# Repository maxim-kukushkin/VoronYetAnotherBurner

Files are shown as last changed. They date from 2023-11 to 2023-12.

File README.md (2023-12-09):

# Description

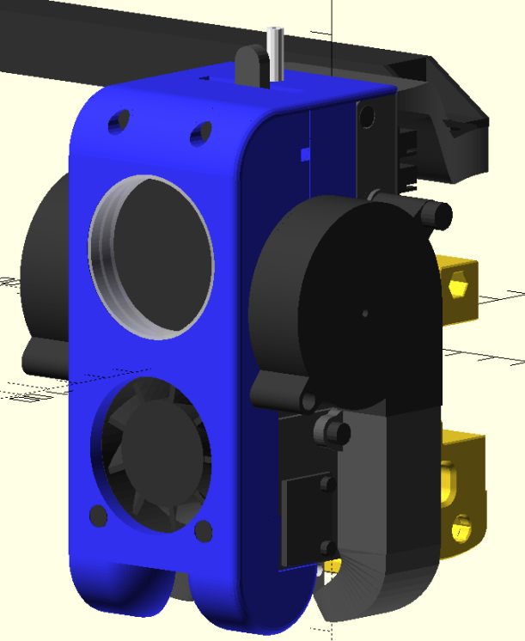
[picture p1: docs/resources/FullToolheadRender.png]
Full assembly render


YetAnotherBurner is (as the name suggests) yet another attempt to design a toolhead for Voron Trident (and 2.4) 3D printers. The main concern the author had about the existing solutions are:
- Usage of custom extruders
- Lack of attention to the part cooling (making it impossible to print PLA overhangs with the printer doors closed)
- Lack of LEDs or Trident support in some of the alternative projects

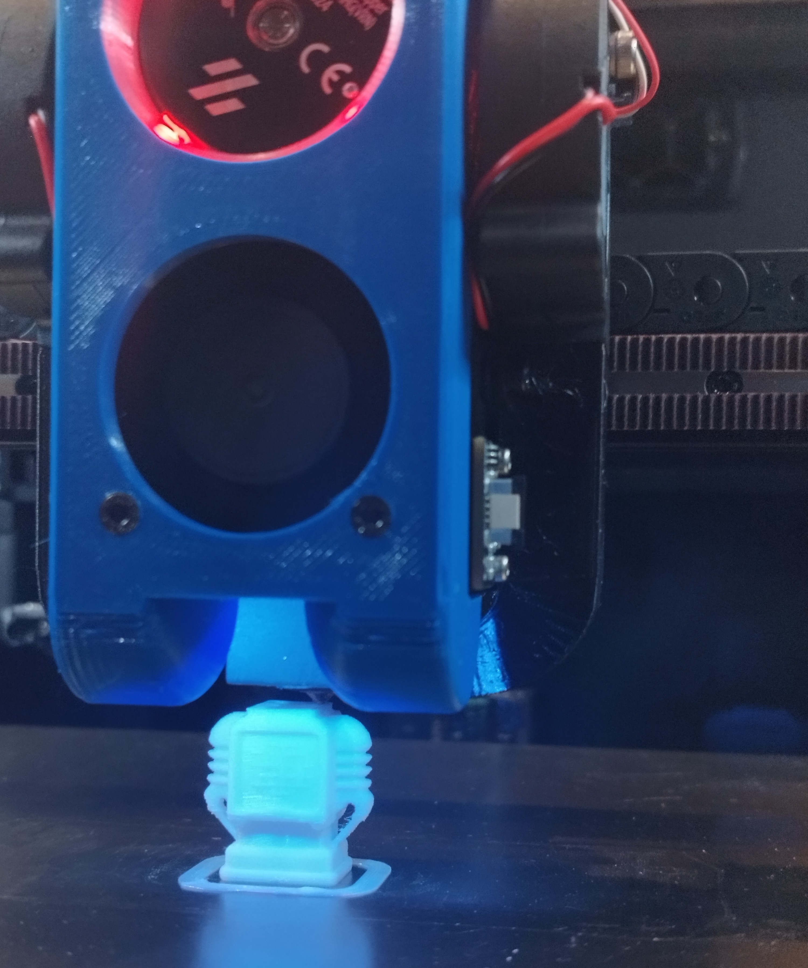
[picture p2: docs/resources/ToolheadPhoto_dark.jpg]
Toolhead photo (dark)


The features of this solution are:
- Strong part cooling (using 2x 5015 blower fans)
- Support of LEDs (2x part highlight + 4x status LEDs at the top)
- Usage of an existing extruder (BondTech LGX Lite)
- Easy loading of the filament + good grip of the bowden tube (by the extruder itself)
- Support of the toolhead breakout PCBis (same PCBs as used in Stealthburner)
- Support of ADXL345 accelerometer mounting
- Doesn't interfere with KlickyProbe, so it can be used as normal with this toolhead

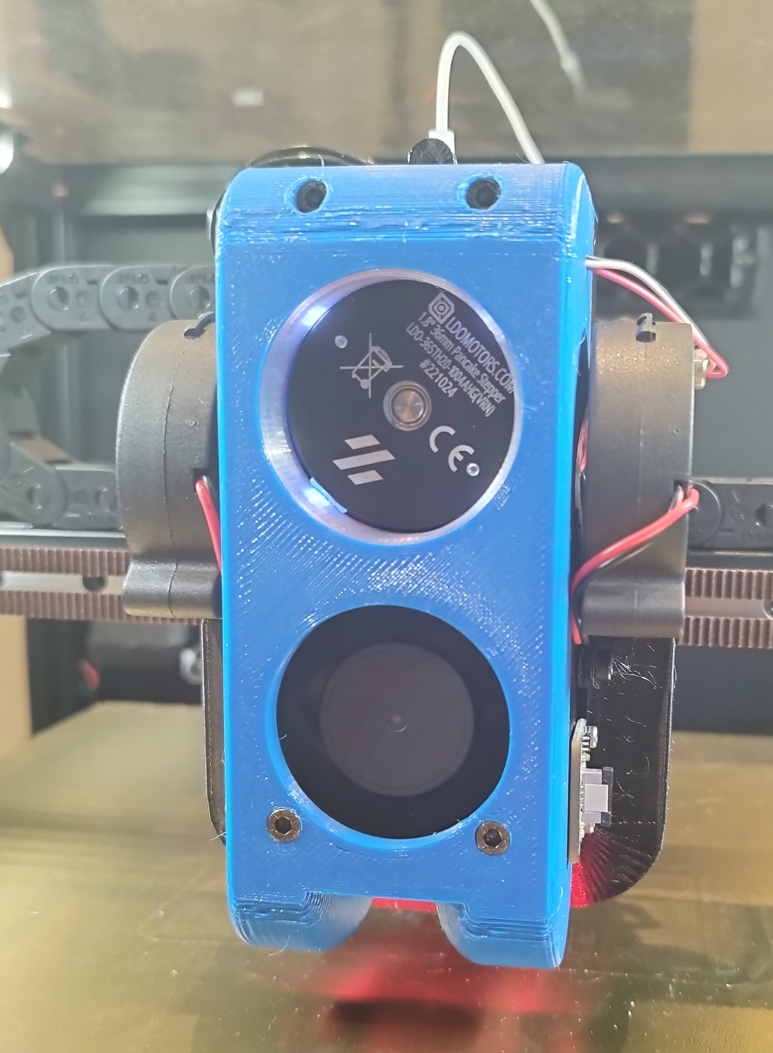
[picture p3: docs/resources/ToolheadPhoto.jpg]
Toolhead photo


The toolhead uses BondTech LGX Lite extruder and currently only supports Dragon High Flow hotend. It is also based on Stealthburner's X Frame mounts (so migration from Stealthburner should be more or less straightforward).

### Known drawbacks
- Due to the size of the toolhead along X-axis there's a limit on the toolhead's travel in the front corners (Y=0) of the printer. Y-axis, for example, needs to be homed first in case the toolhead is positioned around Y=0
- As of the time of writing no support of alternative hotends or accelerometers

## BOM
See the [BOM document](docs/BOM.md)

## Assembly
See the [Assembly manual](docs/Assembly.md)

## Klipper settings

The following Klipper settings are recommended for usage of this toolhead.

The settings listed here indicate what needs to be adjusted, it's not the complete config. So use it as a reference, don't Ctrl-C/Ctrl-V.

### `printer.cfg`
```
[extruder]
rotation_distance: 5.69395   # Bondtech 5mm Drive Gears
microsteps: 16
full_steps_per_rotation: 200 # 200 for 1.8 degree, 400 for 0.9 degree

[probe]
x_offset: 0
y_offset: 19.75
z_offset: 6.39 # !! starter point, this needs to be further adjusted for each individual build

[neopixel headlight]
chain_count: 6
color_order: GRB
```

### `stealthburner_leds.cfg`
```
[gcode_macro _sb_vars]
variable_logo_idex: "1,2,5,6"
variable_nozzle_idx: "3,4"
```

## Development
The OpenSCAD models included as source files rely on [NopSCADlib](https://github.com/nophead/NopSCADlib). In order to be able to open them and render the model in OpenSCAD one needs to install it first.

On Linux it's done by following a couple of simple steps:

1. `mkdir -p cd ~/.local/share/OpenSCAD/libraries`
2. `cd ~/.local/share/OpenSCAD/libraries`
3. `git clone https://github.com/nophead/NopSCADlib.git`

Once, it's done everything should be ready. The following are the main files:

- `FullModel.scad` - the complete model with all the screws, heat inserts and other parts. Due to specifics of NopSCADlib, it renders slowly (up to 30 seconds), so, please, be patient :)
- `common.scad` - common constants and functions that are used among multiple files 
- `ToPrint` - contains all the parts that need to be printed in order to assemble this toolhead, and which are part of this toolhead
- `ToPrint/DragonHF` - contains the parts specific to the Dragon HighFlow hot end. In future, there might be other cartidges added in case of demand.
- `lib` - some extra common "library" functions to help rendering/calculating things like screws, heat inserts, etc.

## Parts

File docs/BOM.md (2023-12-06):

## Below is the list of the components and tools that are needed to build the toolhead

### Devices
- Dragon High Flow hotend
- BondTech LGX Lite extruder
- 2x 5015 blower fans (24V, but check your printer's voltage!)
- 1x 4010 fan (24V, but check your printer's voltage!)
- 6x ws2812b RGB LEDs
- (optional) ADXL345 accelerometer
- (optional, but recommended) LDO toolhead breakout PCB

### Screws (allen cap head)
- 2x M2x6
- 4x M2.5x16
- 6x M3x6
- 4x M3x8
- 6x M3x12
- 2x M3x16
- 6x M3x20
- 2x M3x30
- 2x M3x50
- 2x M4x20

### Washers
- 2x M3 (in theory, optional)

### Heatset inserts
- 2x M2x3.5x3.5 (or M2x3.5x3)
- 22x M3x5x4
- 2x M4x6x4

### Other
- PTFE tube ~30mm length (better to have some extra), 4mm outer diameter, ~1.8mm inner diameter (to use between the extruder and the hotend)
- Bowden tube (to guide the filament into the extruder)
- 3x awg 26-30 wires, preferably different colors, ~50cm each (better to have some extra) (for LEDs)
- Molex Micro-Fit 3.0 male (this is what LDO kits use, it may vary based on what LED connector is already being used in the printer)
- For JST-XH 2-pin splitter:
  - 2x JST-XH 2-pin female plugs
  - 1x JST-XH 2-pin male plug
  - 2x awg 26-30 wires (ideally red and black), ~10cm each
  - (optional, but highly recommended) Heat shrink tubes matching the wires in diamter
- (optional) 3x JST-XH 2-pin connectors (to shorten fan wires and ensure better cablework)
- 1x JST-XH 4-pin connector (for extruder's motor, in case LDO Breakout PCB is used)

### Tools
- Soldering iron + solder
- PETG filament (normal color, accent color and transparent filament). Option to use ABS, but it hasn't been tested with the STLs/models included in this repo
- (optional) soldering iron adaptor for heatset inserts
- A crimping tool would come in handy when working with the connectors
- A screwdriver for M2, M2.5, M3 and M4 allen keys

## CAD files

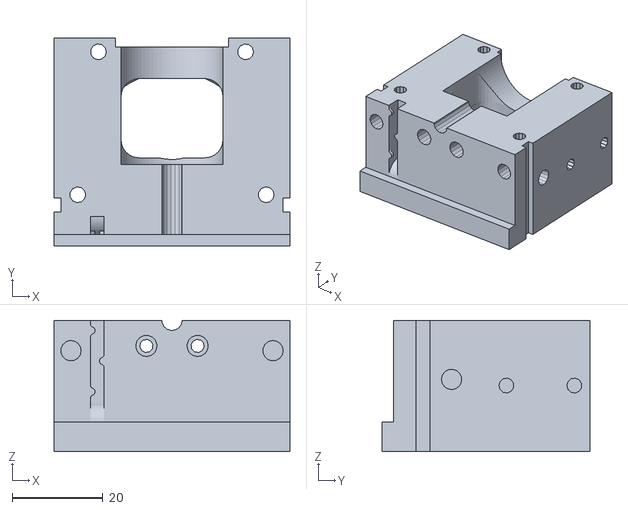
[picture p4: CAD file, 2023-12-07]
ToPrint/DragonHF/stls/HE_cartridge_front.stl
52.1 x 46.0 x 29.0

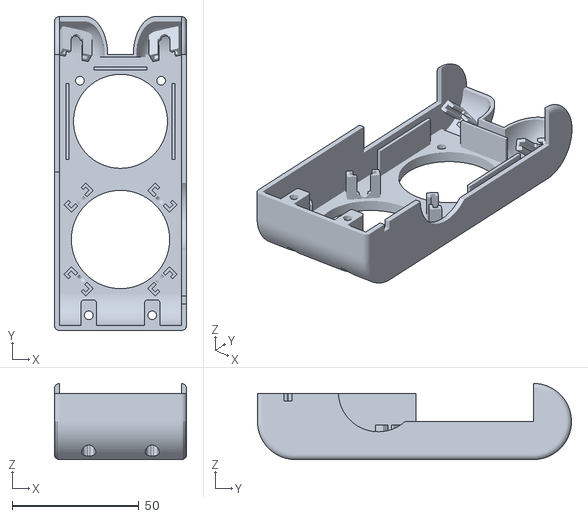
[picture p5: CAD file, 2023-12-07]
ToPrint/stls/[a]_FrontCover.stl
52.1 x 123.7 x 30.0

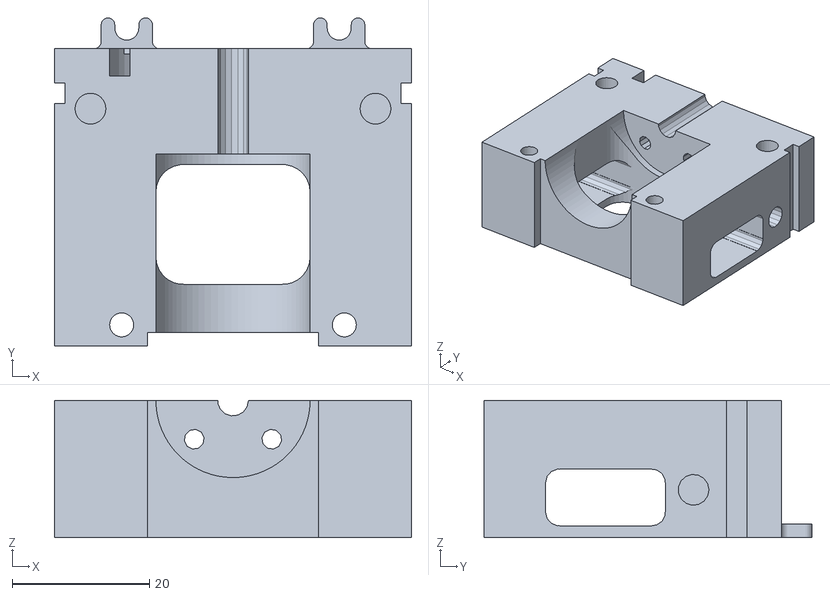
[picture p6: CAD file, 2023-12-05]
ToPrint/DragonHF/stls/HE_cartridge_back.stl
52.1 x 47.9 x 20.0

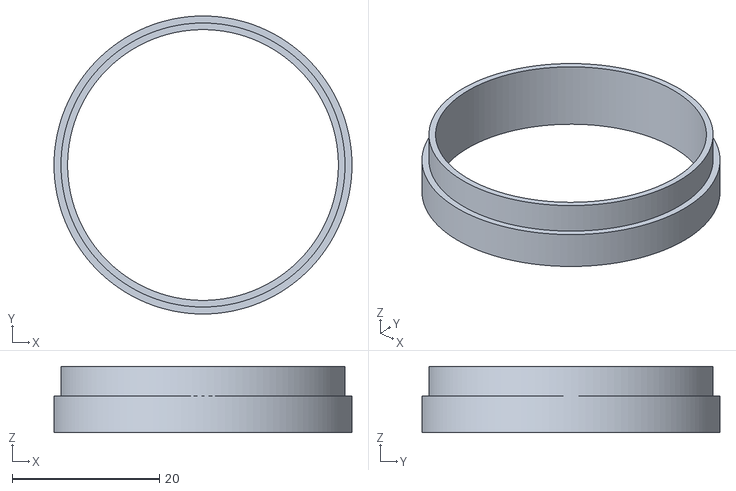
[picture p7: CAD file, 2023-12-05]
ToPrint/stls/[c]_MotorWindowInsert.stl
40.5 x 40.5 x 9.00

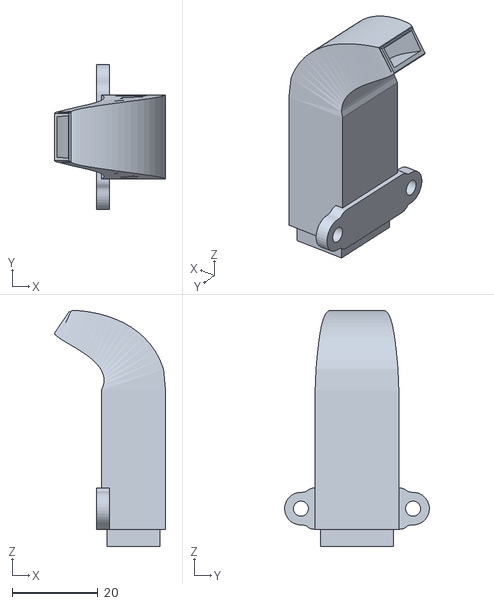
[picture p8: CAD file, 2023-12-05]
ToPrint/stls/CoolingDuct_x2.stl
25.8 x 33.6 x 54.9

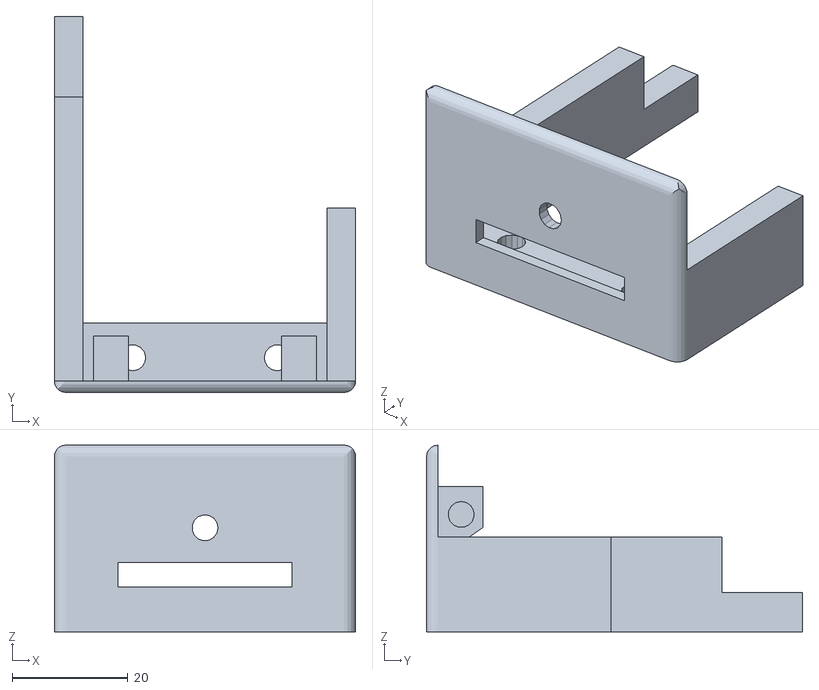
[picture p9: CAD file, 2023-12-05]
ToPrint/stls/[a]_TopCover.stl
52.1 x 65.0 x 32.3

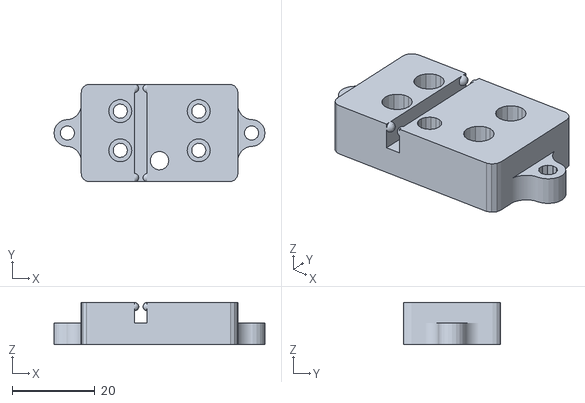
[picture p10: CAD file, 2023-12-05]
ToPrint/stls/ExtruderMount.stl
51.1 x 23.6 x 10.2

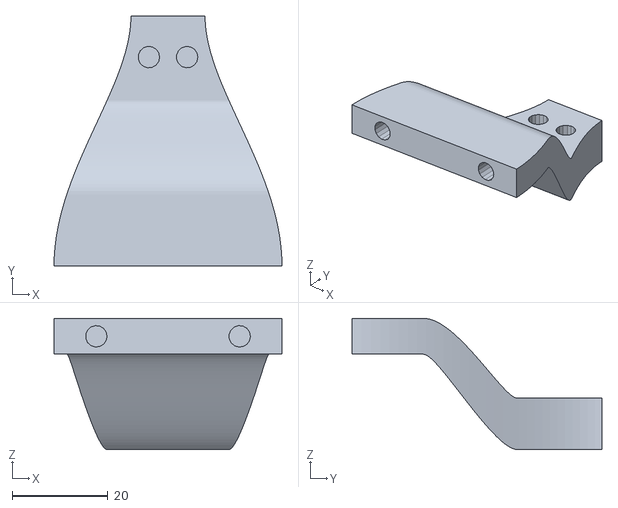
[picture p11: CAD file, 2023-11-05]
ToPrint/stls/DragChainHolder.stl
47.7 x 52.3 x 27.4

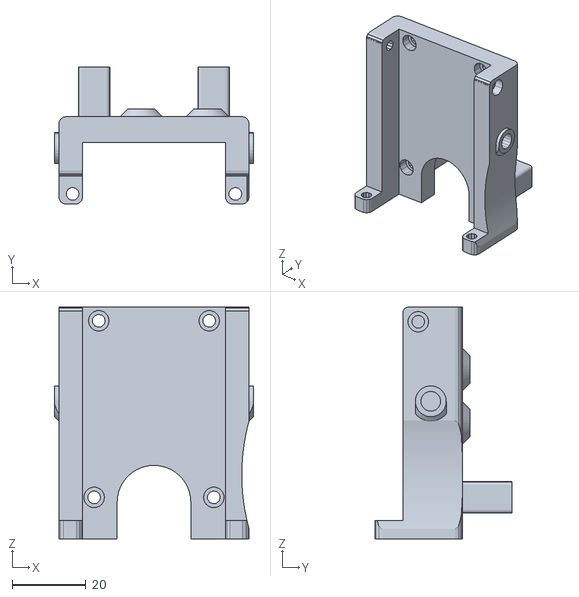
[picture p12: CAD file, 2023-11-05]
ToPrint/stls/PCB_Bracket.stl
54.1 x 37.3 x 63.0

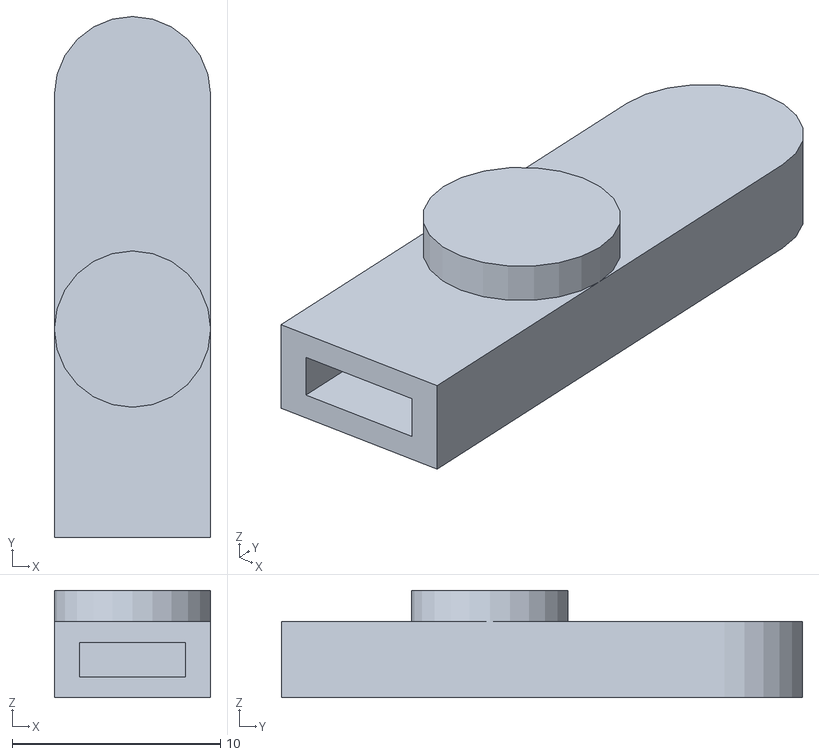
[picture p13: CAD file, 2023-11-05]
ToPrint/stls/ExtruderLeverExtension.stl
7.50 x 25.0 x 5.15

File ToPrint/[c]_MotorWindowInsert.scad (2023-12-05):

// [c]_MotorWindowInsert.scad -- contains the model of the Motor Window Insert part of YetAnotherBurner */
// Copyright (C) 2023  Maxim Kukushkin <maxim.kukushkin@gmail.com>

/*
This file is part of YetAnotherBurner.

YetAnotherBurner is free software: you can redistribute it and/or modify it under the terms of the GNU General Public License as published by the Free Software Foundation, either version 3 of the License, or (at your option) any later version.

YetAnotherBurner is distributed in the hope that it will be useful, but WITHOUT ANY WARRANTY; without even the implied warranty of MERCHANTABILITY or FITNESS FOR A PARTICULAR PURPOSE. See the GNU General Public License for more details.

You should have received a copy of the GNU General Public License along with YetAnotherBurner. If not, see <https://www.gnu.org/licenses/>. 
*/

$fs = 1;
$fa = 0.4;

eps = 0.004;

use <../common.scad>

use <../models/BondTech_LGX_Lite.scad>

MotorWindowInsert(for_stl_export = true);

module MotorWindowInsert(for_stl_export = false) {
    inner_d = motor_body_d() + 0.3;
    color([0.8, 0.8, 0.8, 0.7])
        rotate([for_stl_export ? 180 : -90, 0, 0]) {
            linear_extrude(height = cover_front_plate_thickness() + eps)
                difference() {
                    circle(d = motor_body_d() + 2 * cover_motor_insert_w() + 0.1);
                    circle(d = inner_d);
                }

            translate([0, 0, cover_front_plate_thickness()])
                linear_extrude(height = 5)
                    difference() {
                        circle(d = motor_body_d() + 2 * cover_motor_insert_inner_w());
                        circle(d = inner_d);
                    }
        }
}

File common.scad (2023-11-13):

// common.scad -- contains all constants and calculations shared among the modules of YetAnotherBurner */
// Copyright (C) 2023  Maxim Kukushkin <maxim.kukushkin@gmail.com>

/*
This file is part of YetAnotherBurner.

YetAnotherBurner is free software: you can redistribute it and/or modify it under the terms of the GNU General Public License as published by the Free Software Foundation, either version 3 of the License, or (at your option) any later version.

YetAnotherBurner is distributed in the hope that it will be useful, but WITHOUT ANY WARRANTY; without even the implied warranty of MERCHANTABILITY or FITNESS FOR A PARTICULAR PURPOSE. See the GNU General Public License for more details.

You should have received a copy of the GNU General Public License along with YetAnotherBurner. If not, see <https://www.gnu.org/licenses/>. 
*/

include <NopSCADlib/lib.scad>
include <NopSCADlib/vitamins/fans.scad>
include <NopSCADlib/vitamins/blowers.scad>

use <models/DragonHF_Hotend.scad>
use <models/BondTech_LGX_Lite.scad>

use <lib/2d_shapes.scad>
use <lib/screws.scad>
use <lib/heat_inserts.scad>

function extruder_mount_screw_offset() = m3_screw_cap_d() / 2 + 0.5;
function extruder_mount_screw_dist() = extruder_body_length() + extruder_mount_screw_offset() * 2;

function HE_cartridge_location() = [0, 0, -HE_cartridge_top_offset()];
function HE_location() = [0, -20, -18.4];
function HE_cartridge_front_location() = extruder_mount_location();

function HE_cartridge_blower_wire_ch_offset_z() = 6.5;
function HE_cartridge_blower_wire_ch_depth() = 1.5;
function HE_cartridge_blower_wire_ch_width() = 3;

function HE_cartridge_cooler_wire_ch_offset() = 16.5;
function HE_cartridge_cooler_wire_ch_depth() = 4;
function HE_cartridge_cooler_wire_ch_w() = 3;
function HE_cartridge_cooler_wire_ch_holder_h() = 0.8;
function HE_cartridge_cooler_wire_ch_holder_l() = 3;
function HE_cartridge_cooler_wire_ch_holder_w() = 1;
 
function HE_cartridge_roof_h() = HE_cartridge_h() - hotend_heatsink_h();
function HE_cartridge_floor_h() = 4;
function HE_cartridge_slot_h() = 1.5;
function HE_cartridge_screw_h() = 9.5;
function HE_cartridge_w() =
    extruder_mount_screw_dist() + m3_heat_insert_d() + 2 * heat_insert_min_offset();
function HE_cartridge_h() = -HE_location().z - HE_cartridge_top_offset() + hotend_heatsink_h();
function HE_cartridge_depth() = 50 + m3_cap_h() - 4;
function HE_cartridge_bottom_screw_offset() = 2;
function HE_cartridge_outer_h() = HE_cartridge_h() + HE_cartridge_bottom_screw_offset();
function HE_cartridge_top_offset() = 3;

function HE_cartridge_vent_shaft_rounding() = 4;
function HE_cartridge_vent_w() = hotend_heatsink_d() + 0.5;
function HE_cartridge_vent_h() = hotend_heatsink_h() - HE_cartridge_slot_h() - HE_cartridge_floor_h() - 3;
function HE_cartridge_back_depth() = abs(HE_location().y);
function HE_cartridge_front_depth() = HE_cartridge_depth() - HE_cartridge_back_depth();

function HE_cartridge_common_screw_offset_z() = 5 + 2 + m3_screw_d($for_cutting = false) / 2;
function HE_cartridge_common_screw_dist() =
    HE_cartridge_w() - m3_heat_insert_d() - 2 * heat_insert_min_offset() - 3;


function HE_fan_to_bottom_offset() = 4;
function HE_fan_location() = [
    0,
    -HE_cartridge_depth() - fan_depth(fan40x11) / 2,
    -HE_cartridge_h() - HE_cartridge_top_offset() + HE_fan_to_bottom_offset() + fan_width(fan40x11) / 2];

function PTFE_shaft_d() = 4.2;
function PTFE_shaft_cut_d() = 4.5;

function bottom_mount_screw_dist() = 32.5;
function bottom_mount_screw_z_offset() = 43.3;

function top_holding_screw_dist() = 31;

function top_mount_screw_dist() = 32.5;
function top_mount_screw_z_offset() = 8.3;
function top_mount_screw_y_offset() = 7.8;

function extruder_mount_shaft_offset() = extruder_mount_side_wall() + PTFE_shaft_d() / 2;
function extruder_mount_h() = m3_cap_h() + m3_washer_h() + 7;
function extruder_mount_side_wall() = 3;
function extruder_mount_w() =
    extruder_mount_side_wall() + PTFE_shaft_d() / 2 + mounting_screw_to_hole_w_offset2() + m3_washer_d() / 2 + extruder_mount_side_wall();
function extruder_mount_location() =
    [HE_location().x, HE_location().y, HE_cartridge_location().z];
function extruder_mount_loop_w() = m3_screw_d() + 2 * 1.5;
function extruder_mount_vertical_cut_offset() = extruder_mount_loop_w() / 2 + 2;

function extruder_mount_wire_ch_offset() = 4.5;

function extruder_location() =
    [extruder_mount_location().x, extruder_mount_location().y, extruder_mount_location().z + extruder_mount_h()];

function pcb_bracket_backplate_offset_y() = 14;
function pcb_bracket_backplate_thickness() = 7;
function pcb_bracket_backplate_h() = 63;
function pcb_bracket_bottom_mount_thickness() = 5;
function pcb_bracket_rounding() = 2;
function pcb_bracket_location() = [
    extruder_mount_location().x,
    extruder_mount_location().y + extruder_mount_shaft_offset() - extruder_mount_w() / 2,
    extruder_mount_location().z];
function pcb_bracket_side_wall_dist() = extruder_body_length() + 0.7;
function pcb_bracket_side_wall_thickness() = (HE_cartridge_w() - pcb_bracket_side_wall_dist()) / 2;

function pcb_bracket_pcb_spacing() = 2;
function pcb_bracket_cover_mount_screw_offset_z() = 4;
function pcb_bracket_cover_mount_screw_offset_y() = 5;

function blower_fan_offset_x() = 1.2;
function blower_fan_offset_z() = 8;
function right_blower_intake_w() = blower_bore(RB5015) - 2;
function right_blower_intake_depth() = 2;
function blower_axis_z_offset() = blower_axis(RB5015).y;
function blower_axis_y_offset() = blower_axis(RB5015).x;

function left_blower_location() = [
    -HE_cartridge_w() / 2 - blower_fan_offset_x(),
    extruder_mount_location().y + blower_exit(RB5015) / 2,
    extruder_mount_location().z - blower_fan_offset_z()
];
function right_blower_location() = [
    HE_cartridge_w() / 2 + blower_fan_offset_x() + blower_depth(RB5015),
    extruder_mount_location().y + blower_exit(RB5015) / 2,
    extruder_mount_location().z - blower_fan_offset_z()
];

function drag_chain_w() = 17.2;
function drag_chain_location() = [0, 38, 43.3];
function drag_chain_screw_dist() = 8;
function drag_chain_screw_offset() = 4;

function drag_chain_holder_thickness() = m3_heat_insert_d() + 2 * heat_insert_min_offset();
function drag_chain_holder_screw_dist() = 30;
function drag_chain_holder_location() = [
    0,
    pcb_bracket_location().y + pcb_bracket_backplate_offset_y() + pcb_bracket_backplate_thickness(),
    pcb_bracket_location().z + pcb_bracket_backplate_h() - drag_chain_holder_thickness() / 2
];

function cooling_duct_location() = [
    HE_cartridge_w() / 2,
    HE_location().y,
    right_blower_location().z
];

function blower_shaft_outer_l() = 17;
function blower_shaft_outer_w() = 12.4;
function blower_wall() = 1.24;
function cooling_duct_mount_screw_offset_z() = m3_screw_cap_d() / 2 + 2;
function cooling_duct_mount_l() = blower_shaft_outer_l() + 2 * blower_wall();
function cooling_duct_mount_screw_offset_y() = cooling_duct_mount_l() / 2 + m3_screw_cap_d() / 2 + 0.5;


function accelerometer_w() = 16;
function accelerometer_l() = 20;
function accelerometer_h() = 1.56;
function accelerometer_screw_dist() = 15;
function accelerometer_screw_side_offset() = 2.4;

function cooling_fan_depth() = 11;
function cooling_fan_side() = fan_width(fan40x11);

function cover_top_plate_thickness() = 2;
function cover_front_plate_thickness() = 4;
function cover_split_offset() = 18;
function cover_join_screw_dist() = 25;
function cover_front_mount_screw_offset() = 6;

function cover_color() = "#3333FF";
//function parts_color() = "green";
function parts_color() = "#555555";

function cover_motor_insert_w() = 1;
function cover_motor_insert_inner_w() = 2;

function cover_led_wire_hole_offset() = 10;
function cover_led_wire_hole_side() = 3;

function top_cover_location() = [
    HE_location().x,
    HE_location().y,
    HE_cartridge_location().z + pcb_bracket_backplate_h()
];

function front_cover_location() = [
    top_cover_location().x,
    top_cover_location().y - cover_split_offset(),
    top_cover_location().z
];

module cover_rounded_profile(width, rounding) {
    difference() {
        union() {
            centered_square([width - rounding * 2, rounding * 2]);
            for (i = [-1, 1])
                translate([i * (width / 2 - rounding), 0])
                    circle(r = rounding, $fn=20);
        }

        centered_square([width * 2, -rounding * 2], centerY=false);
    }
}

function motor_window_insert_location() = [
    extruder_location().x,
    HE_cartridge_front_location().y - HE_cartridge_front_depth() - cooling_fan_depth() - cover_front_plate_thickness(),
    extruder_location().z + motor_offset_z()
];

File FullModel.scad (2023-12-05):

// FullModel.scad -- contains a view of the entire view of YetAnotherBurner assembled together */
// Copyright (C) 2023  Maxim Kukushkin <maxim.kukushkin@gmail.com>

/*
This file is part of YetAnotherBurner.

YetAnotherBurner is free software: you can redistribute it and/or modify it under the terms of the GNU General Public License as published by the Free Software Foundation, either version 3 of the License, or (at your option) any later version.

YetAnotherBurner is distributed in the hope that it will be useful, but WITHOUT ANY WARRANTY; without even the implied warranty of MERCHANTABILITY or FITNESS FOR A PARTICULAR PURPOSE. See the GNU General Public License for more details.

You should have received a copy of the GNU General Public License along with YetAnotherBurner. If not, see <https://www.gnu.org/licenses/>. 
*/

include <NopSCADlib/lib.scad>
include <NopSCADlib/vitamins/fans.scad>
include <NopSCADlib/vitamins/blowers.scad>

use <models/BondTech_LGX_Lite.scad>
use <models/DragonHF_Hotend.scad>
use <models/LDO_Toolhead_PCB.scad>

use <lib/screws.scad>
use <lib/heat_inserts.scad>
use <lib/2d_shapes.scad>
use <lib/3d_shapes.scad>

use <common.scad>
use <ToPrint/DragonHF/HE_cartridge_back.scad>
use <ToPrint/DragonHF/HE_cartridge_front.scad>
use <ToPrint/ExtruderMount.scad>
use <ToPrint/PCB_Bracket.scad>
use <ToPrint/DragChainHolder.scad>
use <ToPrint/CoolingDuct_x2.scad>
use <ToPrint/[a]_TopCover.scad>
use <ToPrint/[a]_FrontCover.scad>
use <ToPrint/ExtruderLeverExtension.scad>
use <ToPrint/[c]_MotorWindowInsert.scad>

$fs = 1;
$fa = 0.4;

eps = 0.004;

screw_color = "#333333";

/******
DEVICES
******/

rotate([-90, 0, -90])
    translate([/*Y*/ -164.2, /*Z*/ -131.6, /*X*/-21.6])
        import("3rd_party/x_frame_V2TR_MGN12_left.stl");
        
rotate([90, 0, -90])
    translate([/*Y*/ -164.2, /*Z*/ -168.4, /*X*/-21.6])
        import("3rd_party/x_frame_V2TR_MGN12_right.stl");
        
rotate([0, 0, -90])
    translate([/*Y*/ -175.6, /*X*/ -141.7, -56.5])
        import("3rd_party/KlickyProbe_AB_mount_v2.stl");

translate(extruder_location())
    rotate([0, 0, 180])
        BondtechLGXLite();
    
translate(HE_location())
    rotate([0, 0, 0])
        DragonHF_Hotend($detailed=false);
    
translate(left_blower_location())
    rotate([90, 0, -90])
        blower(RB5015);

translate(right_blower_location())
    rotate([90, 0, -90])
        blower(RB5015);

translate(HE_fan_location())
    rotate([-90, 0, 0])
        fan(fan40x11);

translate(th_pcb_location())
    rotate([90, 0, 180])
        LDO_Toolhead_PCB();

translate(drag_chain_location())
    drag_chain();

translate(accelerometer_location())
    accelerometer();

translate(extruder_location())
    translate([0, 0, extruder_body_height() - 1])
        PTFE_tube(30);

translate(HE_location())
    translate([0, 0, -hotend_ptfe_slot_depth()])
        PTFE_tube(29.7);
        
/*******
Toolhead parts
*******/

translate(HE_cartridge_location()) 
    HE_cartridge_back();

translate(HE_cartridge_front_location())
    translate([0, -0.1, 0])
    HE_cartridge_front();
 
translate(extruder_mount_location())
    ExtruderMount();

translate(pcb_bracket_location())
    PCB_Bracket();

translate(drag_chain_holder_location())
    DragChainHolder();

translate(cooling_duct_location())
    CoolingDuct();
mirror([1, 0, 0])
    translate(cooling_duct_location())
        CoolingDuct();

translate(top_cover_location())
    TopCover();

translate(front_cover_location())
    translate([0, -0.1, 0])
    FrontCover();

translate(extruder_location())
    translate([0, -tension_lever_w_offset(), extruder_body_height() + 1])
        rotate([90, 0, 180])
            ExtruderLeverExtension();

translate(motor_window_insert_location())
    MotorWindowInsert();

/*******
Screws
*******/

color(screw_color) {
    $for_cutting = false;
    // HE cartridge to X carriage (top)
    for (i = [-1, 1])
        translate([i * top_holding_screw_dist() / 2, -HE_catridge_hook_thickness(), 0])
            rotate([90, 0, 0])
                m3_screw(6);

    // HE cartridge to X carriage (bottom)
    for (i = [-1, 1])
        translate([
            i * bottom_mount_screw_dist() / 2,
            -HE_cartridge_depth() + m3_cap_h(),
            -bottom_mount_screw_z_offset()
        ])
            rotate([90, 0, 0])
                m3_screw(50);

    translate(HE_cartridge_front_location()) {
        // HE cartridge front to back mounting
        HE_cartridge_front_for_each_backmount_screw_pos()
            translate([0, m3_cap_h(), 0])
                rotate([90, 0, 0])
                    m3_screw(30);

        // HE fan mounting
        HE_cartridge_front_for_each_fan_screw_pos(top_only = true)
            translate([0, -10 + m3_cap_h(), 0])
                rotate([90, 0, 0])
                    m3_screw(12);

        // Accelerometer mounting
        for_each_accelerometer_screw_pos()
            rotate([0, 90, 0])
                translate([0, 0, accelerometer_h()])
                    m2_screw(6);
    }

    translate(front_cover_location()) {
        // Bottom mounting screws
        front_cover_for_each_bottom_screw_pos()
            translate([0, m3_cap_h(), 0])
                rotate([90, 0, 0])
                    m3_screw(20);

        // Top mounting screws
        front_cover_for_each_top_screw_pos()
            rotate([90, 0, 0])
                m3_screw(20);
    }

    // Extruder mount to HE cartridge
    for (i = [-1, 1])
        translate([
            extruder_mount_location().x + i * extruder_mount_screw_dist() / 2,
            extruder_mount_location().y - extruder_mount_screw_y_offset(),
            extruder_location().z
        ])
            m3_screw(16, with_washer=true);

    // Hotend screws
    translate(HE_location())
        for (i = [0:3])
            rotate([0, 0, 45 + i * 90])
                translate([hotend_screw_offset(), 0, HE_cartridge_screw_h()])
                    m2_5_screw(16);

    // Extruder to extruder bracket screws
    translate(extruder_mount_location())
        for_each_extruder_mount_screw_pos()
            rotate([180, 0, 0])
                m3_screw(12);

    // Cooling duct mount
    for (i = [0, 1])
        mirror([i, 0, 0])
            translate(cooling_duct_location())
                cooling_duct_for_each_screw_pos()
                    rotate([0, 90, 0])
                        m3_screw(6);

    translate(pcb_bracket_location()) {
        // PCB Bracket to X Carriage mounting screws
        pcb_bracket_for_each_mounting_screw_pos()
            translate([0, m3_cap_h(), 0])
                rotate([90, 0, 0])
                    m3_screw(20);

        // Drag chain holder screws
        pcb_bracket_for_each_drag_chain_screw_pos()
            translate([0, m3_cap_h(), 0])
                rotate([90, 0, 0])
                    m3_screw(8);

        // PCB screws
        pcb_bracket_for_each_pcb_mounting_point()
            translate([0, pcb_bracket_pcb_spacing() + th_pcb_thickness(), 0])
                rotate([-90, 0, 0])
                    m3_screw(6);

        // Top cover to PCB bracket mounting screws
        pcb_bracket_for_each_top_cover_mount_screw_pos()
            translate([-m3_cap_h(), 0, 0])
                rotate([0, 90, 0])
                    m3_screw(8);

        // Blower fan mounting screws
        pcb_bracket_for_each_blower_fan_mounting_point()
            translate([blower_fan_offset_x() + blower_depth(RB5015), 0, 0])
                rotate([0, 90, 0])
                    m4_screw(20);
    }
}

/******
Heat inserts
******/

union() {
    translate(top_cover_location()) {
        top_cover_for_each_join_insert_pos()
            rotate([90, 0, 0])
                m3_heat_insert();

        top_cover_for_each_bracket_join_pos()
            rotate([0, 90, 0])
                m3_heat_insert();
    }

    translate(drag_chain_holder_location()) {
        drag_chain_holder_for_each_mount_screw_pos()
            rotate([90, 0, 0])
                m3_heat_insert();

        drag_chain_holder_for_each_chain_screw_pos()
            m3_heat_insert();
    }

    translate(pcb_bracket_location()) {
        pcb_bracket_for_each_pcb_mounting_point()
            translate([0, pcb_bracket_pcb_spacing(), 0])
                rotate([-90, 0, 0])
                    m3_heat_insert();

        pcb_bracket_for_each_blower_fan_mounting_point()
            translate([blower_fan_offset_x(), 0, 0])
                rotate([0, 90, 0])
                    m4_heat_insert();
    }

    translate(HE_cartridge_location()) {
        HE_cartridge_b_for_each_f_heat_insert_pos()
            rotate([90, 0, 0])
                m3_heat_insert();

        HE_cartidge_b_for_each_duct_mount_heat_insert_pos()
            rotate([0, 90, 0])
                m3_heat_insert();
    }

    translate(HE_cartridge_front_location()) {
        HE_cartridge_front_for_each_fan_screw_pos()
            rotate([90, 0, 0])
                m3_heat_insert();
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

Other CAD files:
models/BondTech_LGX_Lite.scad
ToPrint/CoolingDuct_x2.scad
ToPrint/DragChainHolder.scad
ToPrint/DragonHF/HE_cartridge_back.scad
ToPrint/DragonHF/HE_cartridge_front.scad
ToPrint/ExtruderLeverExtension.scad
ToPrint/ExtruderMount.scad
ToPrint/PCB_Bracket.scad
ToPrint/[a]_FrontCover.scad
ToPrint/[a]_TopCover.scad
models/DragonHF_Hotend.scad
models/LDO_Toolhead_PCB.scad
models/ws2812b.scad

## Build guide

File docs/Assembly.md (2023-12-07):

# Printing suggestions
- Layer: 0.2mm
- Filament: PETG
- Part Cooling: for majority of parts (see the **Advice** comments inside each section)
- Supports: for some of the parts (see the **Advice** comemtns inside each section)
- Orientation: all printable STLs have been pre-rotated the way they're advised to be printed

# Assembly

## 1. Hot End cartridge
### 1.1. Dragon High Flow

#### 1.1.1. Print the files
Start by printing the hot end cartridge parts from the respective [subdirectory](../ToPrint/DragonHF/stls)

#### 1.1.2. Add heatset inserts to the front part
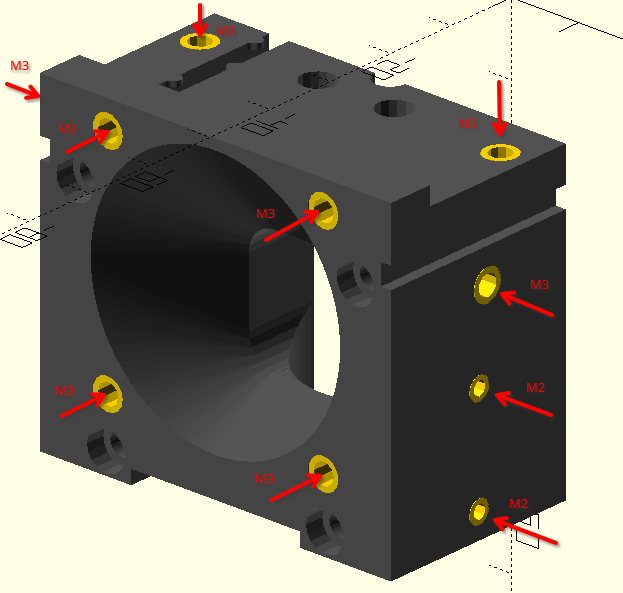
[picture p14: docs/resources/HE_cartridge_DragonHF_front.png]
HE cartridge front with heatset inserts


#### 1.1.3. Add heatset inserts to the back part
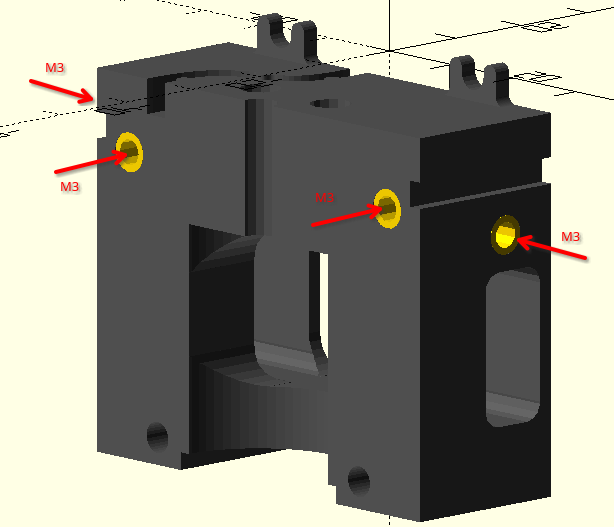
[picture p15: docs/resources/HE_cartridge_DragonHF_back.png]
HE cartridge back with heatset inserts


#### 1.1.4. Cut PTFE tube
It needs need to be as precise as possible to 29.7mm length. An advice to use calipers to mark the length and a sharp knife to do a right-angle cut.
This is one of the important points to ensure smooth and easy loading of filament

#### 1.1.5. Mount the hotend to the back part

- **Make sure that the heater block is facing the front (see the picture)**
- Use 2x M2.5x16 screws to mount the HE to the back part of the cartridge
  There's no much preference to the direction of the wires (of the heater cartridge and the thermistor), however, the advice is to leave them, on the right.
  Also, please, keep in mind that the wires will be routed first straight in the direction of positive Y and then will go straigh up, behing the assembled hotend cartridge.
- Insert the PTFE tube and make sure it fits into the HE's slot

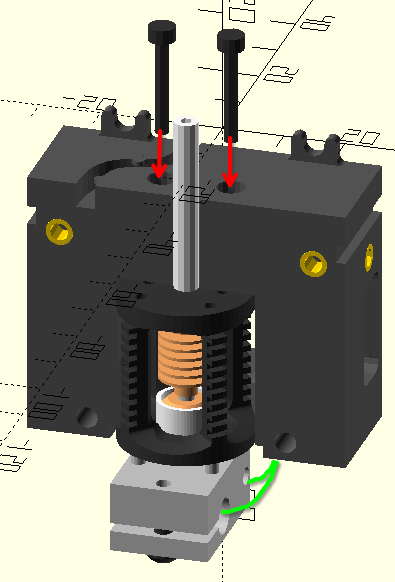
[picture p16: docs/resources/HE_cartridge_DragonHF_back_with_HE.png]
HE cartridge back with HE


#### 1.1.6. Mount the front of the HE cartridge
- Use 2x M3x20 screws to mount the front part of the HE cartridge (don't tighten yet)
- Push PTFE tube a little bit, to double check that it's still in place, pushed into the HE's slot
- Tighten the screws
- Use 2x M2.5x16 screws to attach the HE to the front part of the cartridge

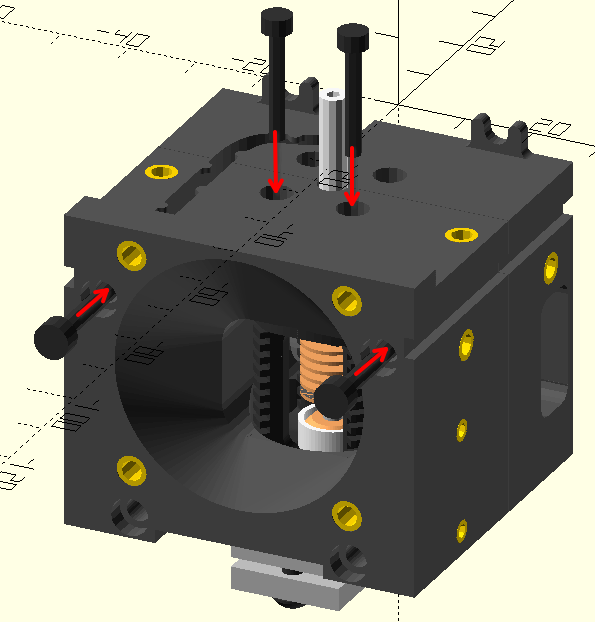
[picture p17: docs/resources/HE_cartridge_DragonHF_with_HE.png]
HE cartridge with HE


#### 1.1.7. Attach the cooling fan
(the screenshots use 40x11 fan because the NopSCADlib didn't have 40x10, but in reality the 40x10 one must be used)

- Use 2x M3x12 screws to attach the cooling fan to the HE cartridge (top only!)
  - Make sure the wires face up
  - Make sure the screw caps fit into fan's slots for them, so that they don't stick above the surface
- Guide the wires throw the channel as pictured below
  - Make sure they are below the surface, cause later other parts will be mounted on top
- You may want to shorten the wires of the fan (by cutting and crimping them) so that the cablework is neater

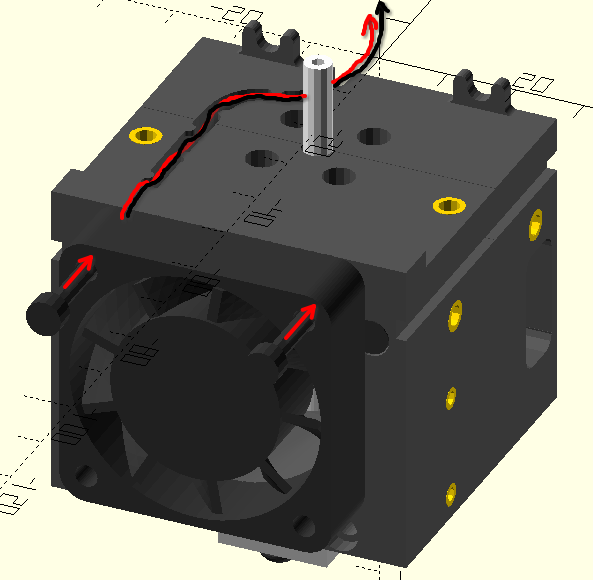
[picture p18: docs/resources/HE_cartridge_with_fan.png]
HE cartridge with fan


## 2. Attach the Hot End cartridge to the X-carriage

### 2.1. Top screws
It's time to attach it to the printer. Use 2x M3x6 screws to initially fix the assembled cartridge on the X-carriage

Make sure the heater cartridge's and thermistor's wires are guided through the shaft available in the X-carriage. It may require a bit of bending of the wires.

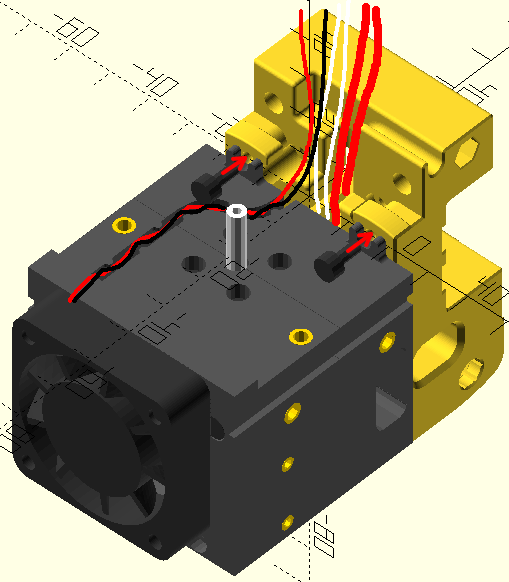
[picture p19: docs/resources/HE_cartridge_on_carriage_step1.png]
HE cartridge on X-carriage, step 1


### 2.2. Bottom screws
Now use 2x M3x50 screws to completely fix the cartridge

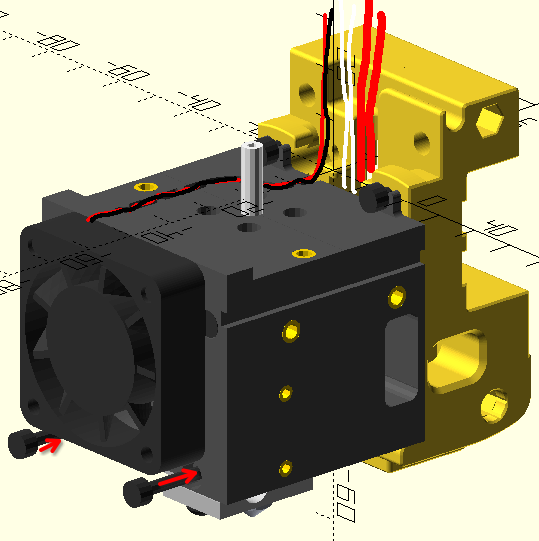
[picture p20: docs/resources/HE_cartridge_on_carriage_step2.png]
HE cartirdge on X-carriage, step 2


## 3. Assemble the PCB bracket

### 3.1 Print the bracket
[PCB Bracket STL](../ToPrint/stls/PCB_Bracket.stl) - **Advice:** use support touching build plate

### 3.2. Add heatset inserts
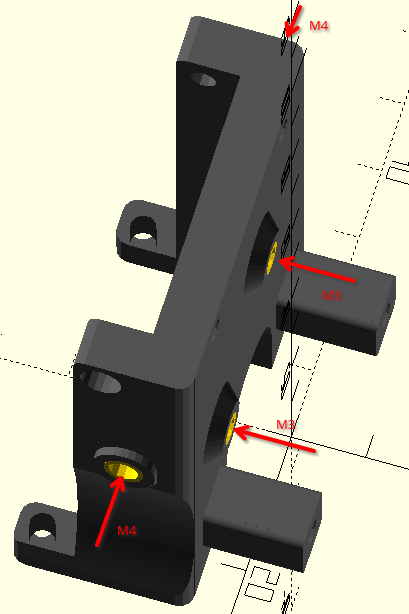
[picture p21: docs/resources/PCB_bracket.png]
PCB Bracket with heatset inserts


### 3.3. Attach the PCB
Use 2x M3x6 screws to attach the PCB (sorry for OpenSCAD's rendering artifacts)

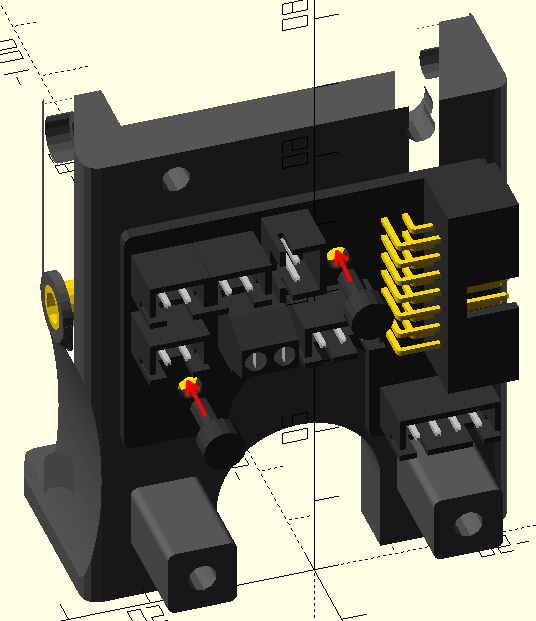
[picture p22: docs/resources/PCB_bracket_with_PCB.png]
PCB Bracket with PCB


## 4. Attach the PCB bracket to X-carriage

Use 2x M3x20 screws to attach the assembled bracket to the X-carriage. Pay attention to the fan wires - they shouldn't be squeezed between the parts

After that it's ok to attach the wires of the fan, heater cartridge and thermistor to the PCB

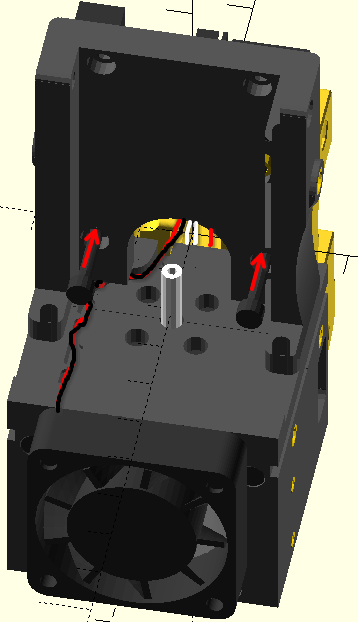
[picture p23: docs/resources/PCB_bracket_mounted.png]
PCB Bracket mounted


## 5. Extruder

### 5.1. Print the parts
[Bracket STL](../ToPrint/stls/ExtruderMount.stl) - **Advice:** use support touching build plate

[Lever Extension STL](../ToPrint/stls/ExtruderLeverExtension.stl) - **Advice:** switch off part cooling. It requires very good layer adhesion. Non-ideal bridges shouldn't be a problem, bad layer adhesion will be.

### 5.2. Extruder's connector
Most probably your BondTech LGX Lite's motor comes with a different connector or no connector at all.
In this step, shorten the wires of the motor (be careful, scroll the manual further to get an idea of routing of the motor's wires and thus what the length should be) and use a crimping tool to fit a 4-pin JST-XH connector.

### 5.3. Attach the extruder to the bracket
- Use 4x M3x12 screws to attach the extruder to its bracket
- Guide the wires throught the channel in the bracket as shown on the picture
  - Make sure that the wires are below the surface, as the part will attached tightly to another one later

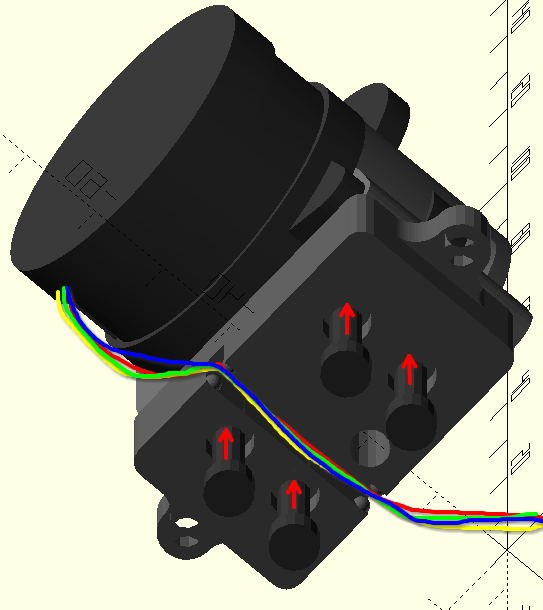
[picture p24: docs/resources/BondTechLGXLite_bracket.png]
BondTechLGXLite bracket


### 5.4. Attach the tensioning lever extension
This one will be later used to move the lever when the toolhead is fully assmebled.
It may seem to not fit too tight, but it won't be problem: due to the small knob it won't go anywhere after the extruder is covered with the top cover.

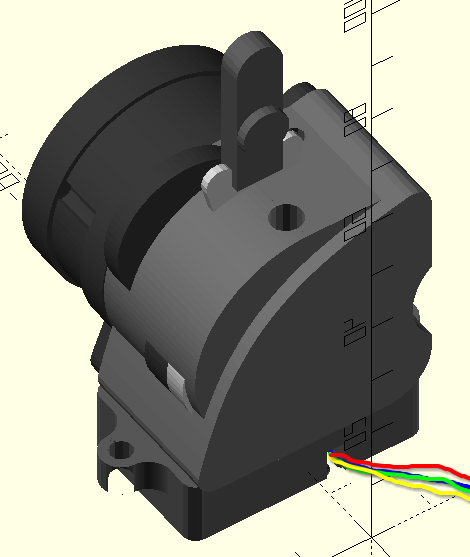
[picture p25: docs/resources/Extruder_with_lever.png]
Extruder with lever


### 5.5. Attach the bowden tube
Choose between 2 options

#### If using one single bowden tube between the spool and the toolhead
*This is the original Stealthburner's/Voron's design, where one single bowden tube goes from the filament spool outside the printer, all the way into the toolhead*

If going for this option:

- Perform partial top cover assembly by following [step 1](#81-print-the-part) and [step 2](#82-add-heat-inserts) there
- Guide the bowden tube through the filament hole in that part
- Leave the top cover hanging on the bowden tube for now
- Properly fix the bowden tube in the extruder (it normally comes with all needed parts)

#### If using a short bowden tube
*This is the case when the toolhead has a short "tension relief" bowden tube, but the filament hangs in the air inside the printer*

Cut the bowden tube to your liking (~50-60mm recommended) and properly fix it in the extruder (it normally comes with all needed parts)

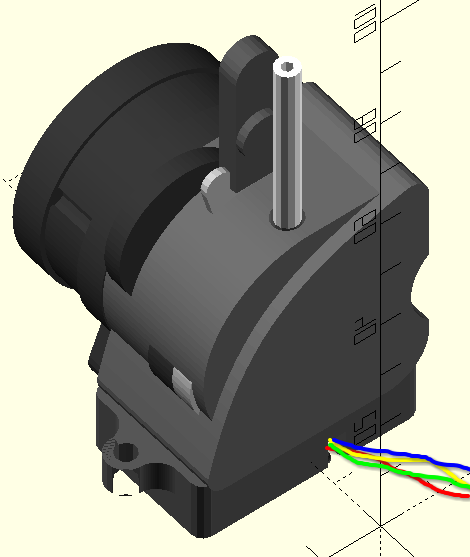
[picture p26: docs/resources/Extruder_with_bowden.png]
Extruder with bowden


### 5.6. Attach the exturder to the toolhead
- Use 2x M3x16 screws (optionally with washers) to attach the assembled extruder, through the PCB bracket loops, to the toolhead.
- Guide the motor's wires through the arc in the PCB bracket and connect to the PCB
- Double check that neither fan's nor motor's wires are squeezed between the parts

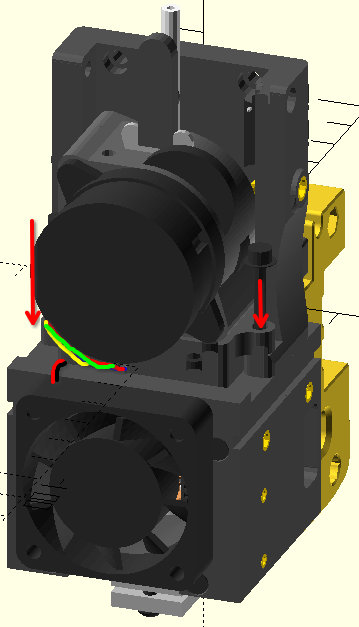
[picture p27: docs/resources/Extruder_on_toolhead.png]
Exturder on the toolhead


## 6. Part cooling fan splitter
Most probably your Breakout PCB (at least LDO's one) comes with a single connector for the part cooling fan. As this setup uses 2 fans, a splitter is needed.

- Solder ~6cm of wires to two female JST-XH plugs, following the same color scheme as the PCB's connector
- (optionally, but recommended) Cover the soldered contacts with the heat shrink tubes
- Use a crimping tool to connect together 2 wires of the same color and attach the JST-XH terminal to them
- Insert the crimped wires into the male JST-XH plug, following the +/GND polarity
- Connect the splitter to the Breakout PCB

## 7. Drag Chain Holder

### 7.1. Print the part
[Drag Chain Holder STL](../ToPrint/stls/DragChainHolder.stl) - **Advice:** use support touching build plate

### 7.2. Add heatset inserts
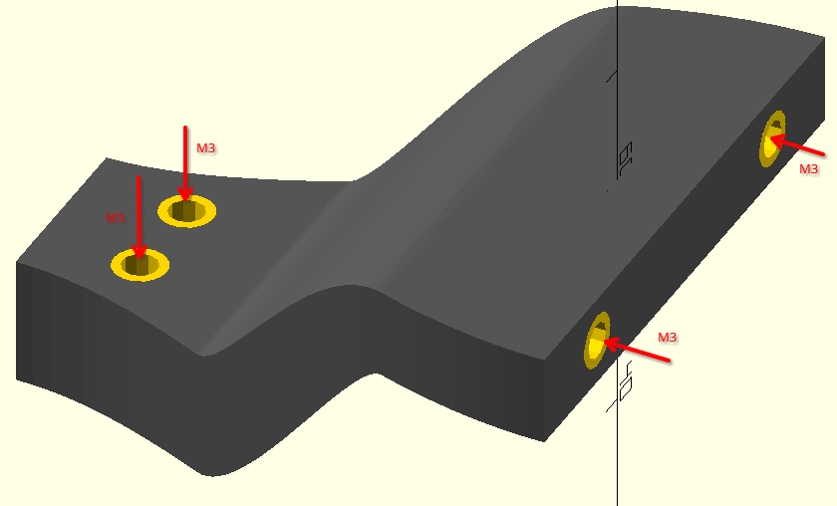
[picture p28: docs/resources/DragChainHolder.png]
Drag Chain Holder with heatset inserts


### 7.3 Attach the drag chain
- Use 2x M3x8 to attach the drag chain holder to the toolhead
- Use the stock M3 screws to attach the drag chain to the holder
- Connect the main MicroFit connector from the drag chain to the PCB

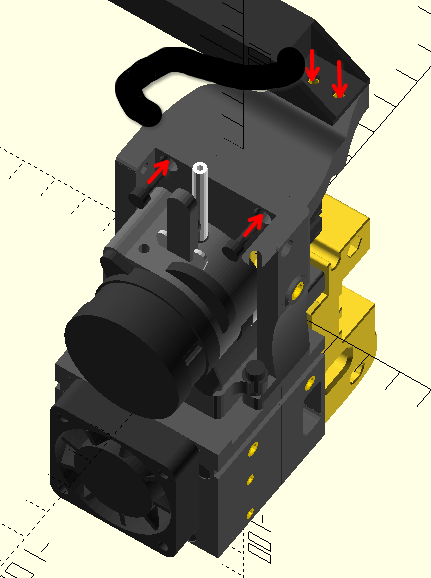
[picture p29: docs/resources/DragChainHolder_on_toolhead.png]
Drag Chain Holder on the toolhead


## 8. Top Cover

### 8.1. Print the part
[Top Cover STL](../ToPrint/stls/[a]_TopCover.stl) - **Advice:** use support touching build plate

### 8.2. Add heatset inserts 
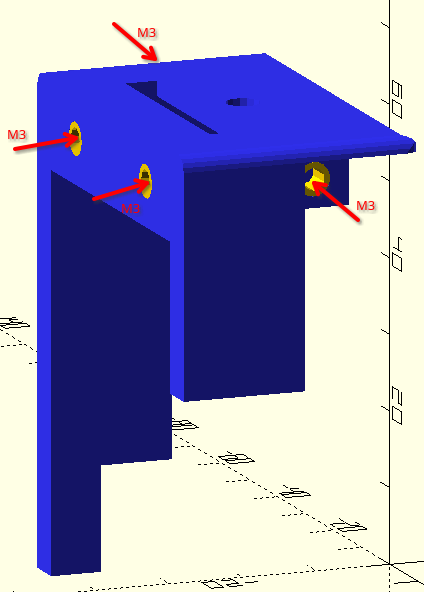
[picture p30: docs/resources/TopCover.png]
Top Cover with heatset inserts


### 8.3. Attach to the toolhead
- Fit the top cover from the top, guiding the bowden tube and the extruder's lever throught the respective holes
- Use 2x M3x8 screws to fix the top cover in place

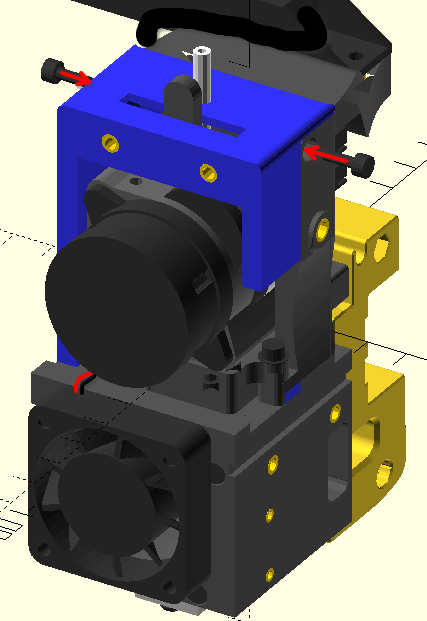
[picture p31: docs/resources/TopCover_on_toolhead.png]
Top Cover on the toolhead


## 9. Front Cover and LEDs

### 9.1. Print the parts
[Front Cover STL](../ToPrint/stls/[a]_FrontCover.stl) - **Advice:** use support touching build plate. The rounding is not ideal. Please, feel free to raise an issue with suggestions.

[Motor Window Insert STL](../ToPrint/stls/[c]_MotorWindowInsert.stl) - as indicated in the file name, this part need to be print using a transparent filament, so that the light from the LEDs is visible

### 9.2. Insert the ring into the panel
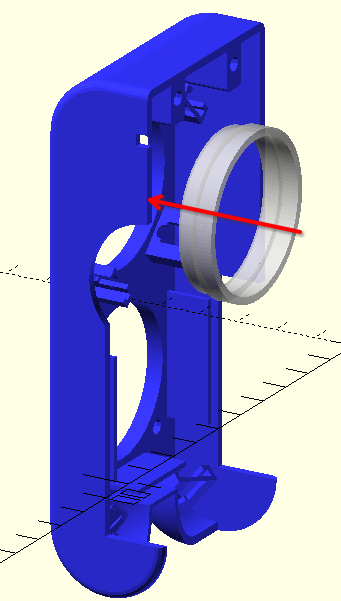
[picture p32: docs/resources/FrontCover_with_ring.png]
Front Cover with ring


### 9.3. Solder LEDs
6 LEDs need to be soldered into a single strip in order to be then inserted into the front cover.
Observe the markings on the LEDs and follow the directions shown on the photo.

Pay attention to the wire colors. One the photo: red - 5v, black - Gnd, white - Data.

- Solder the wires, making sure there's enough length (see the hints on the photo)
- Use a crimping tool to add a 3-pin MicroFit connector (pay attention to the wire positions, double check with Voron's female connector)

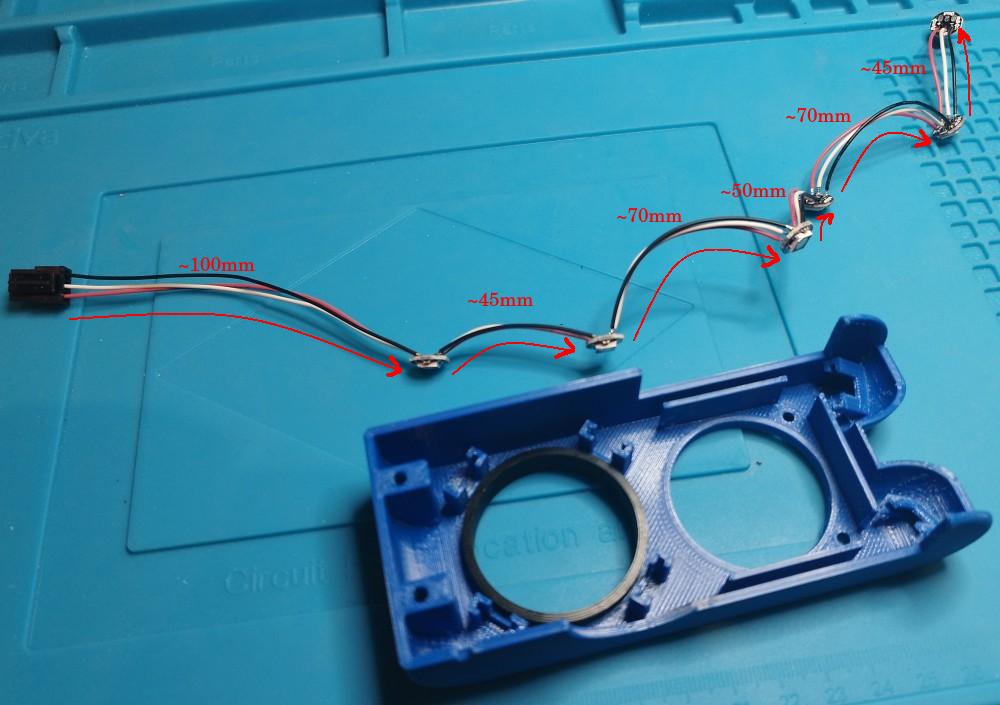
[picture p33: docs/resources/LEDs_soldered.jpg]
Soldered LEDs


### 9.4. Insert LEDs into the panel
Fit the LEDs into their respective slots as shown on the photo

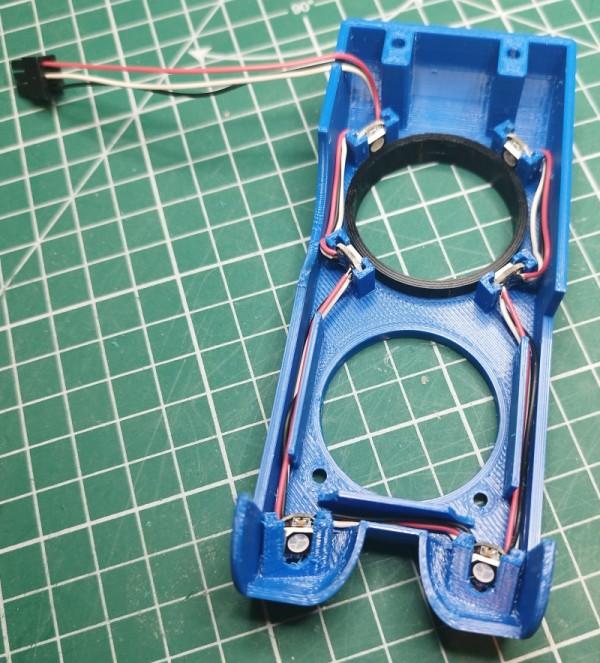
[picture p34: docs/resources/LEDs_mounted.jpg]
Mounted LEDs


### 9.5. Fit the front cover onto the toolhead
- Slide the assembled part from the front onto the toolhead
    - A slight push may be needed so that the ring fits the motor and the fan fits the guides on the panel
    - There's a small collision with the motor wires, but they should have enough space to bend slightly
    - Make sure that the LED wires with the connector are guided through the respective hole in the panel
- Use 4x M3x20 screws to fix the cover in place
- Connect the LED strip to the respective connector of the printer

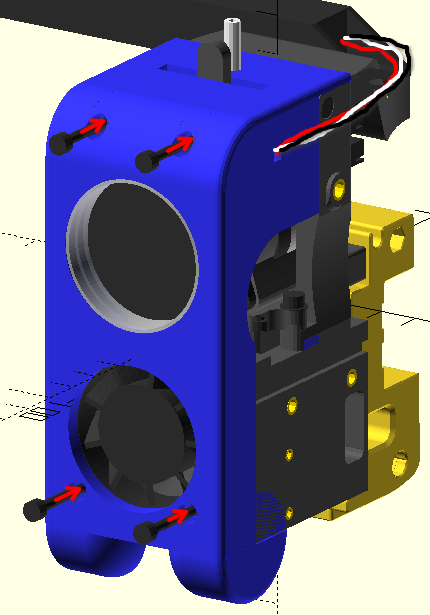
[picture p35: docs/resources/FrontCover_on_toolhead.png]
Front cover on the toolhead


## 10. Part cooling ducts

### 10.1. Print the parts
[2x Cooling Duct STL](../ToPrint/stls/CoolingDuct_x2.stl) - **Advice:** print both together; use support touching build plate

### 10.2. Attach to the toolhead
- Use 4x M3x6 screws (2 on each side) to attach the cooling ducts

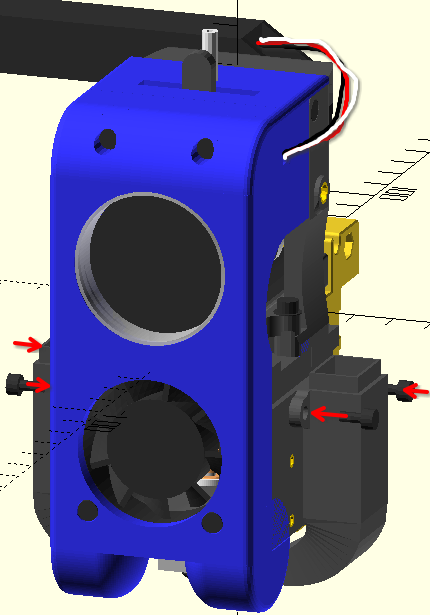
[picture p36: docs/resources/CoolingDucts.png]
Part cooling ducts on the toolhead


## 11. Blower fans
- Slide the blower fans on both sides from the top (they should fit tightly on the ducts)
  - The left blower will have the fan facing outside
  - The right blower will have the fan facing inside. The toolhead parts intentionally have cuts and spacing to ensure proper air intake.
- Try to guide the wires through the channels on the Hotend cartridge to make them less visible
- Use 2x M4x20 screws (1 on each side) to attach the blower fans to the toolhead (the top hole only)
- Connect the blower fans to the splitter made in [the previous step](#6-part-cooling-fan-splitter)

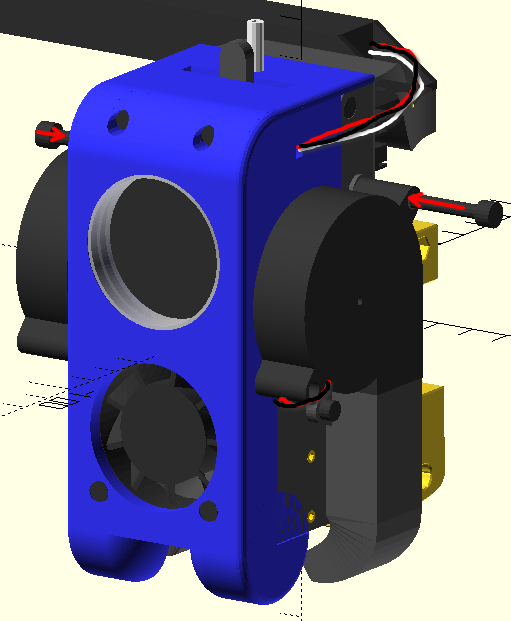
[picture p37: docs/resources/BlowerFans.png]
Blower fans on the toolhead


## 12. Accelerometer
Use 2x M2x6 screws to attach the ADXL345 accelerometer

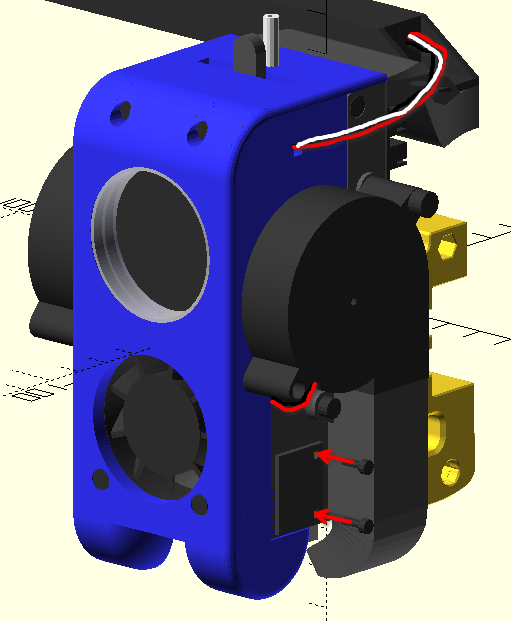
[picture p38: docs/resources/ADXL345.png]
ADXL345 on the toolhead


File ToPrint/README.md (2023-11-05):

The files here follow the same naming convention as in the main Voron Design project

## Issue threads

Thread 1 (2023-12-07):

Add Klipper settings to the Readme

maxim-kukushkin, 2023-12-07:
This hotend requires a couple of small adjustments to the Klipper config that need to be explicitly listed in the Readme:
- Approximate nozzle location in relation to the probe (X/Y only. Z must be tuned individually anyway)
- BondTech LGX Lite settings
- LED configuration

maxim-kukushkin, 2023-12-09:
Added the settings to the `README.md` in the latest commit

Closed 2023-12-09.

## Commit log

2023-11-05 Added STL versions of the printed parts
    [CoolingDuct_x2.stl, DragChainHolder.stl, ExtruderLeverExtension.stl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]
2023-11-05 Added a README for the printed parts folder
2023-11-05 Added the initial readme description
    [FullModel.scad]
2023-11-07 Added BOM. Restructured documents and resources. Removed some commented leftovers in the code
    [[a]_TopCover.scad]
2023-11-07 Updated the BOM
2023-11-12 Added some screws to the full model for better understanding of their location and sizes
    [CoolingDuct_x2.scad, DragonHF_Hotend.scad, FullModel.scad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]
2023-11-12 Added full model screws for the cooling ducts and the extruder
    [CoolingDuct_x2.scad, ExtruderMount.scad, FullModel.scad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]
2023-11-13 Finished adding screws to the full model. Updated the rendered picture
    [FullModel.scad, LDO_Toolhead_PCB.scad, PCB_Bracket.scad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]
2023-12-03 Added some heat inserts to the full model for better visualisation
    [DragChainHolder.scad, FullModel.scad, [a]_TopCover.scad]
2023-12-03 Finished adding all heat sinks to the full model
    [FullModel.scad, HE_cartridge_back.scad, HE_cartridge_front.scad]
2023-12-03 Added source code description. Added a file and reference to assembly instructions
2023-12-04 Started writing the assembly instructions
    [FullModel.scad]
2023-12-04 Typo fixes in the assembly manual
2023-12-05 Finished writing the assembly instructions. Some internal links are still broken
    [FullModel.scad, [a]_FrontCover.scad]
2023-12-05 Added printing settings. Added an option for assembly with a single bowden tube
2023-12-05 Pre-rotated all STLs the way they're advised to be printed
    [CoolingDuct_x2.scad, CoolingDuct_x2.stl, ExtruderMount.scad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]
2023-12-06 Typo fix in BOM
2023-12-07 Slightly refactored screw slot cutting code to make sure reduce the need for support
    [HE_cartridge_front.scad, HE_cartridge_front.stl, PCB_Bracket.scad]
2023-12-07 Extra refactoring to reduce support dependency
    [[a]_FrontCover.scad, [a]_FrontCover.stl]
2023-12-09 Added essential Klipper setting to the README
